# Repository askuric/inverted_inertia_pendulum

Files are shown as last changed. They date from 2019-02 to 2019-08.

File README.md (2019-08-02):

# Inertia Wheel Inverted Pendulum Project 

This project is suitable for anyone with extra free time and passion for interesing projects, but especially for electrical engineering studets (contorl theory students) to learn the control approach of an unstable process and test their algorithms, the primary contorller used in this project is LQR.  

This project is also available on [Thingiverse](https://www.thingiverse.com/thing:3422949)

This project is based on Nucleo STM32F411RE microcontroller. And the repo contains :
- CubeMX project 
- Keil project
- Solidworks files and STLs

YouTube link:<br>
 IMAGE ALT TEXT HERE (https://www.youtube.com/watch?v=POPPNbzDYbw)
 
The full gallery of the project can be found on [Link](https://photos.app.goo.gl/RDtYy89tumxfFMtH9):
<p>


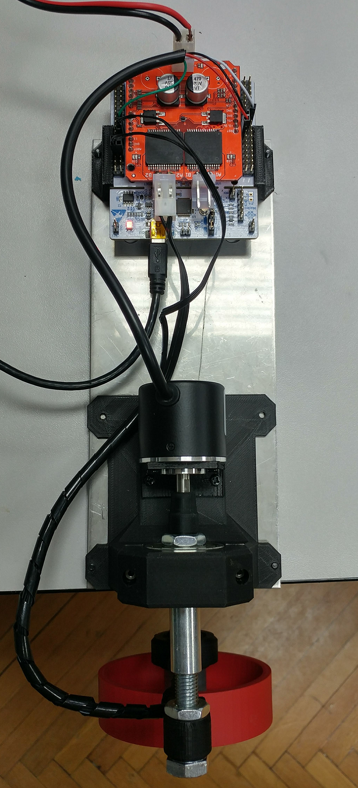
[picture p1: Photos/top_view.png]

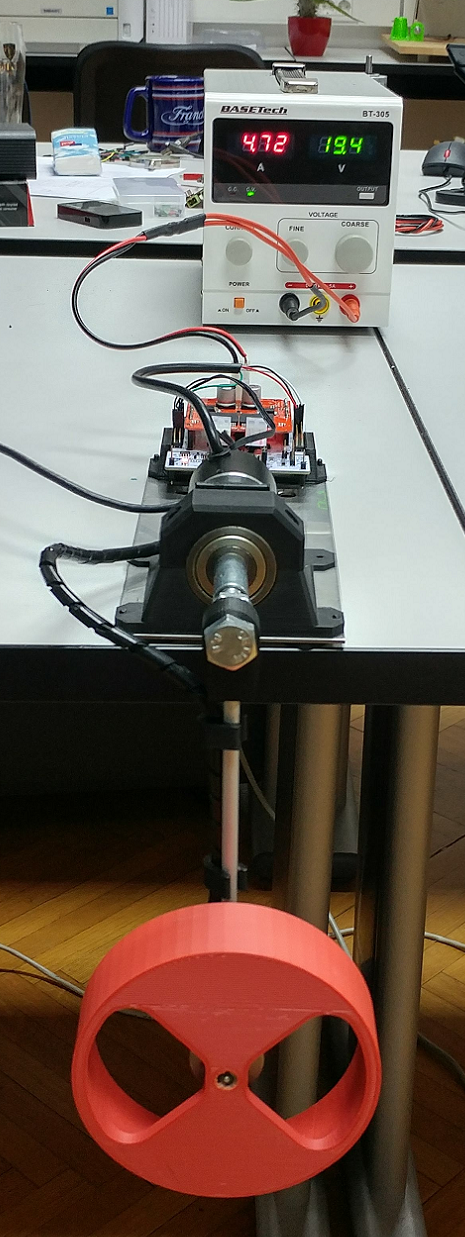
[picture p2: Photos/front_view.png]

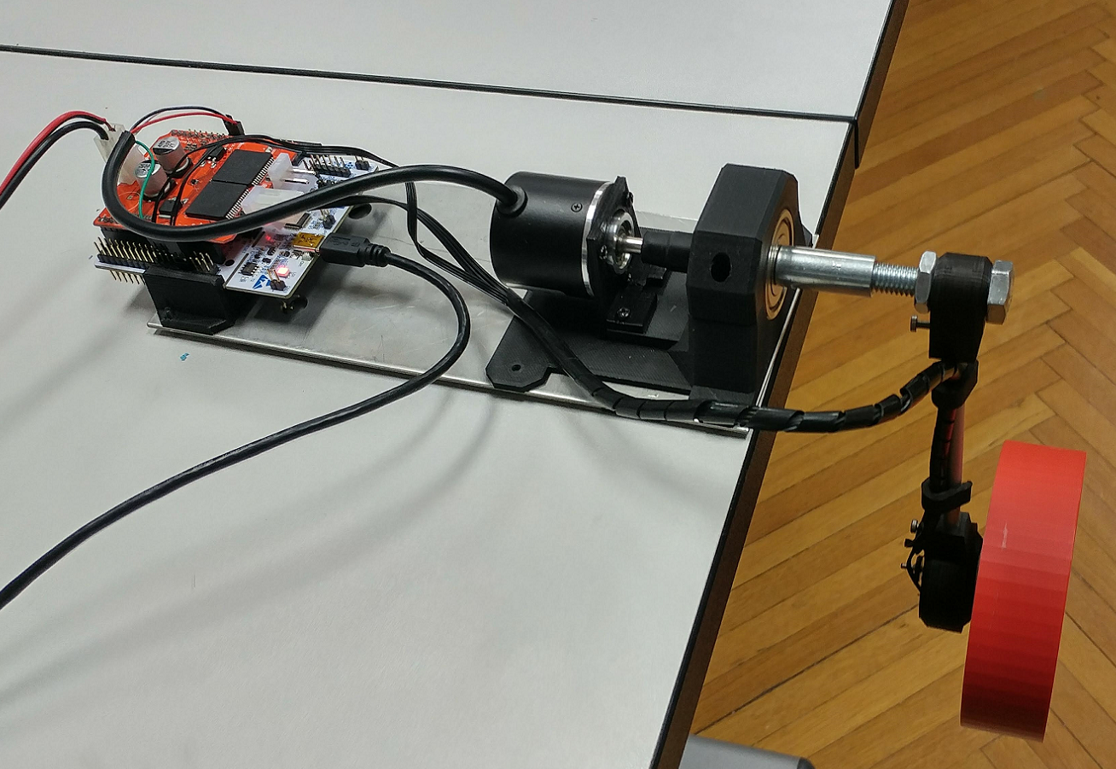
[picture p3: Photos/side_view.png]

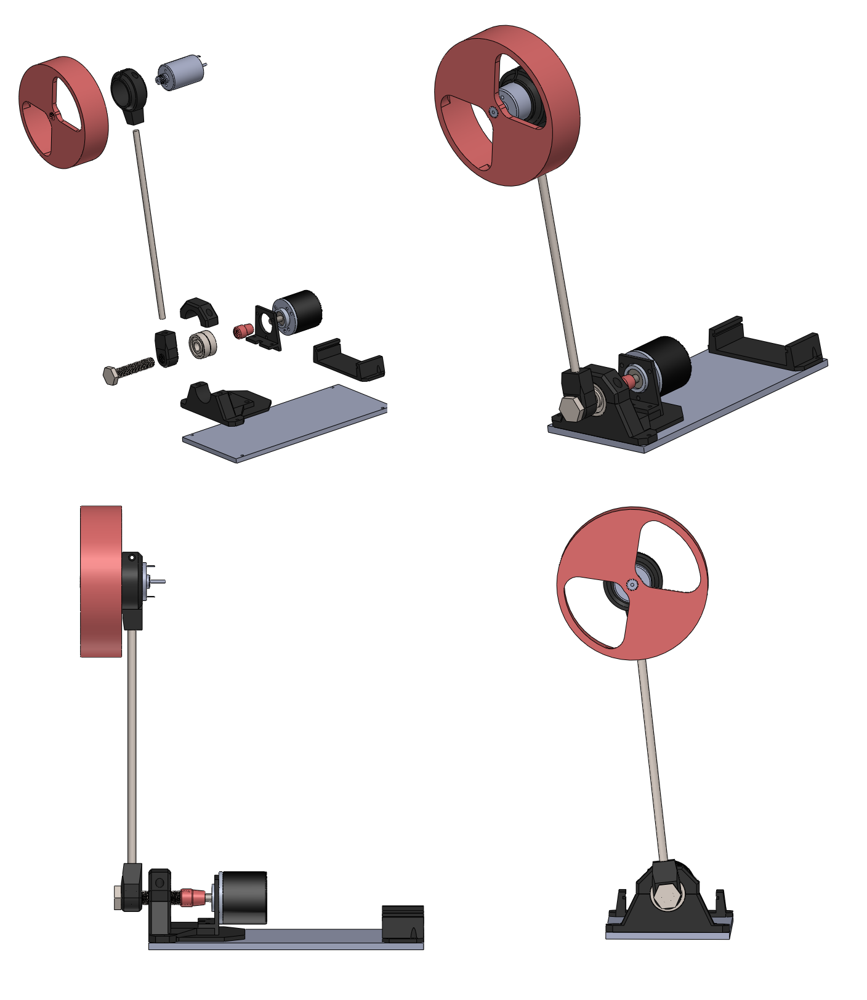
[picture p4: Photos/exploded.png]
</p>

# Electronics hardware
- Nuceleo STM32F411RE - [Mouser](https://hr.mouser.com/ProductDetail/STMicroelectronics/NUCLEO-F411RE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) 
- Monster motor shield - [Ebay](https://www.ebay.com/itm/L298N-Dual-VNH2SP30-Stepper-Motor-Driver-Module-30A-Monster-Moto-Shield-Replace/112031018900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)
- Motor - Mabuchi RS-385PH with encoder (hall or optical)
  -  With encoder or hall sensors  [Ebay](https://www.ebay.com/itm/RS-385PH-16140-MABUCHI-DC-24V-Motor-for-Printer-Copy-machine/222827327725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)
  -  I used motor without sensor and retrofited it with Hall encoder 20cpr [Ebay](https://www.ebay.com/itm/Pololu-Romi-Encoder-Pair-Kit-12-CPR-3-5-18V-with-Hall-effect-sensor-3542/272789024914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)
- Encoder [Aliexpress](https://www.aliexpress.com/item/360-600P-R-Photoelectric-Incremental-Rotary-Encoder-5-24V-AB-Two-Phases-Shaft/32756209569.html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,searchweb201602_1_10065_10068_319_10059_10884_317_10887_10696_321_322_453_10084_454_10083_10103_10618_10307_10820_10301_10821_10303_537_536_10902,searchweb201603_45,ppcSwitch_0&algo_expid=3179dab4-6711-42f4-8e94-b644142c4211-5&algo_pvid=3179dab4-6711-42f4-8e94-b644142c4211)
- 1x 6mm steel or aluminum rod, 120mm long 
- 1x M10x1.5 screw 
- 2x M10x1.5 nuts
- 10x M3 screw 
- 10x M3 Brass Knurl Nuts [Aliexpress](https://www.aliexpress.com/item/100pcs-Brass-Knurl-Nuts-M3x4mm-L-5mm-OD-Metric-Threaded-insert/1294839803.html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)
- 2x ball bearing, 10mm x 35mm x 11mm 
- steel/amulinum/wooden plate (cca 90mm x 2mm x300mm)

# 3D printed parts
-  Inetria wheel - (0.1mm | 50+%)
   - Motor shaft mount has to be adapted
   - The two provided wheel STLs are for 14tooth and 12tooth version of motors
   - Feel free to make your own version of the inertia wheel with the solidworks file
-  Motor mount - (0.2mm | 30%)
-  Pole shaft connector - (0.1mm | 30%)
-  Shaft adapter - (0.1mm | 30%)
-  Table mount + bearing holder - (0.2mm | 30%)
-  Nucleo mount - (0.2mm | 30%)

# Control algorithm
 - PD (Simple)
 - LQR algorithm (Intermediate) - <b>Included in the software + Synthesis using Matlab scirpt</b>
 - MPC (Advanced) - Suggested use of [muao MPC](http://ifatwww.et.uni-magdeburg.de/syst/muAO-MPC/)

# Connecting the hardware
 - Monster motor shield is mounted on nucleo very simply, as on any Arduino
    - It provides the hardware connections needed and no need for additional jumpers
    - Inertia wheel motor should be connected to motor 2 terminal
    - 18V - 5A power supply should be used to power the shield
 - Encoder connection diagram is as follows:
 
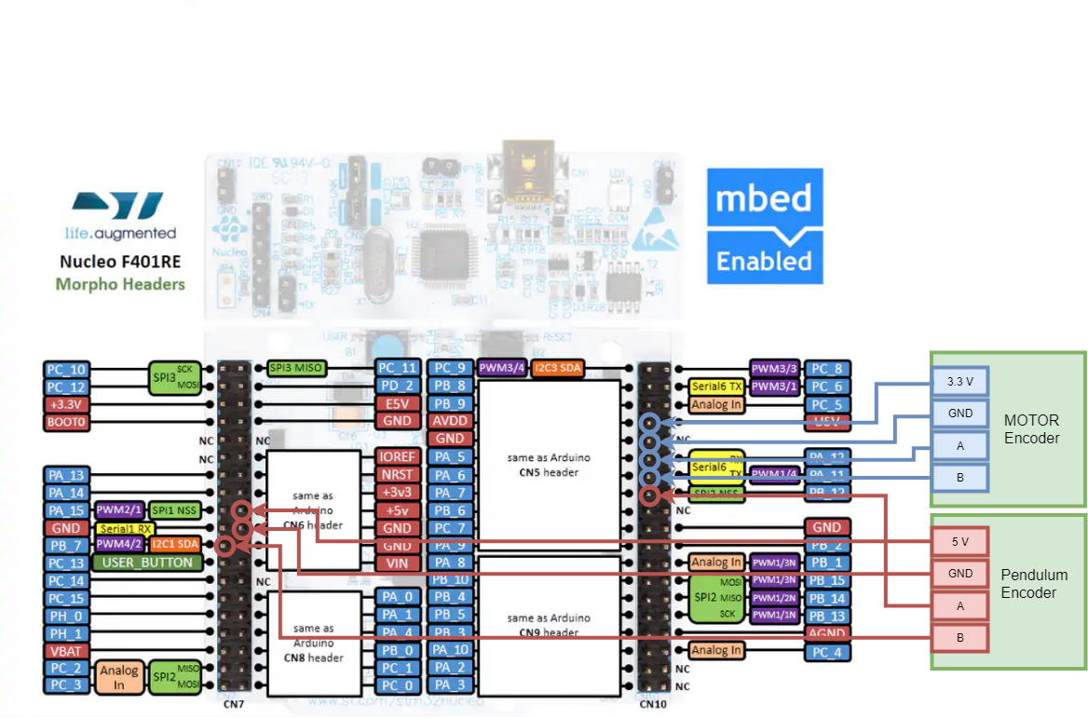
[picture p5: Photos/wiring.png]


# Running the code
 - Build the Keil project and download it to your Nucleo

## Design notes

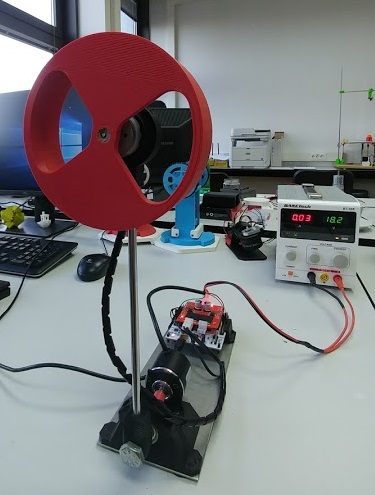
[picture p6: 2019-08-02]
Photos/pendulum3.jpg

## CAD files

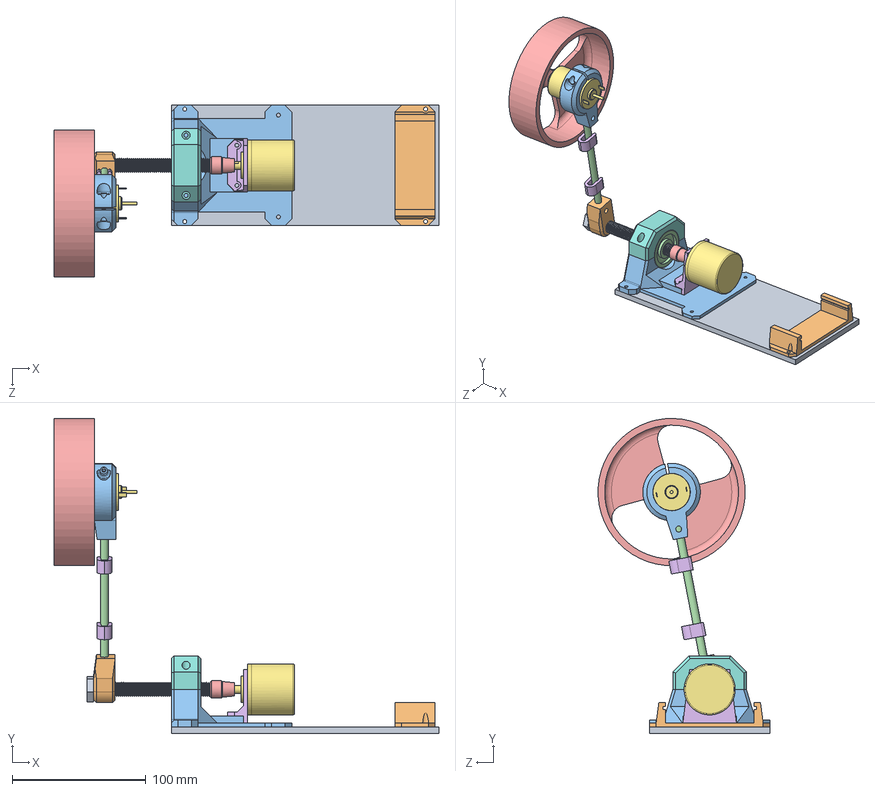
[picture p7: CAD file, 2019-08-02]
CAD/pendulum.SLDASM
287.7 x 235.4 x 128.4 mm
bottom_plate
nucleo_holder
table_mount
radial ball bearing_68_iso x 2
axel_adapter_10mm_encoder
encoder_holder
encoder
bearing_holder
bolt
mount_table_sharft_holder
motor_mout_mabuchi
pole
mabuchi_wheel_14T
cable_holder x 2
MABUCHI RS-385

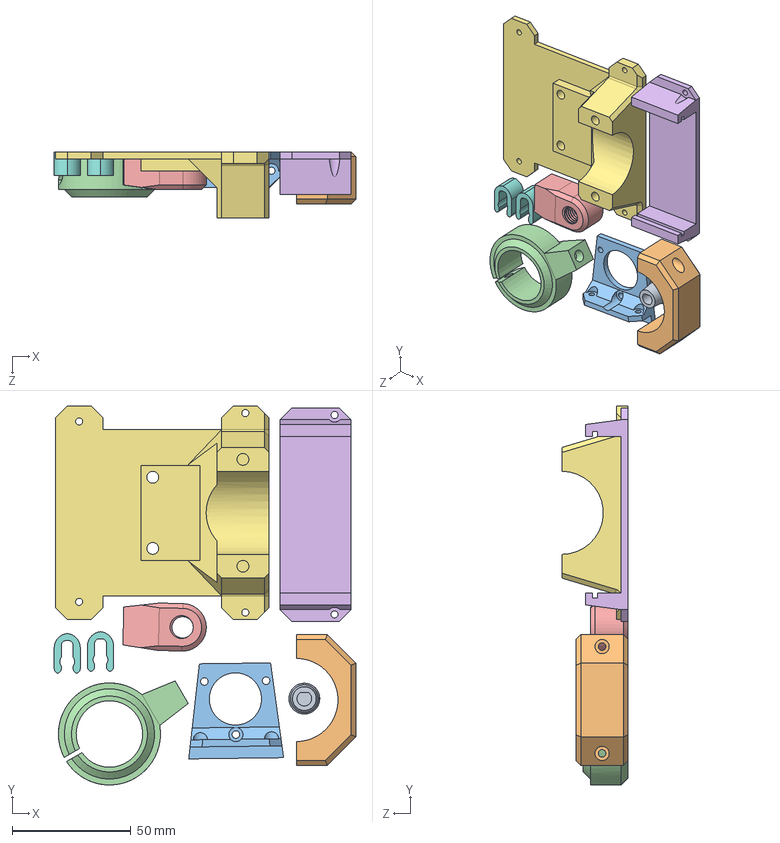
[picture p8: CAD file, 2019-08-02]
CAD/print_layout.SLDASM
127.1 x 159.7 x 28.0 mm
axel_adapter_10mm_encoder
bearing_holder
encoder_holder
motor_mout_mabuchi
mount_table_sharft_holder
nucleo_holder
table_mount
cable_holder x 2

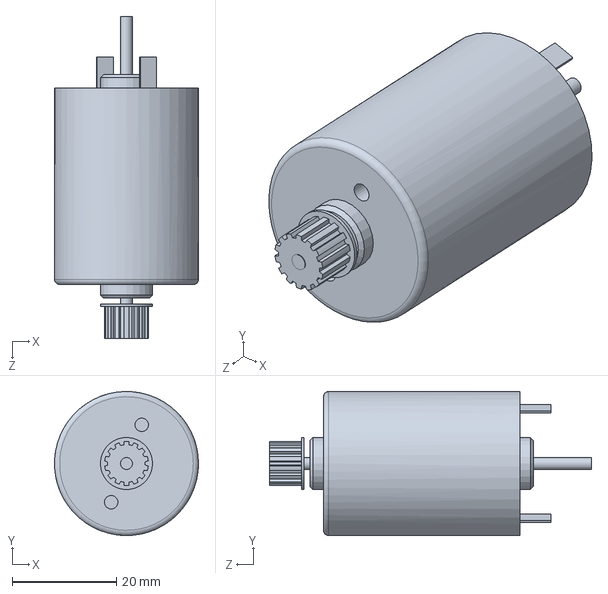
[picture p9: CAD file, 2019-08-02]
CAD/MABUCHI RS-385.SLDPRT
27.7 x 27.7 x 62.0 mm

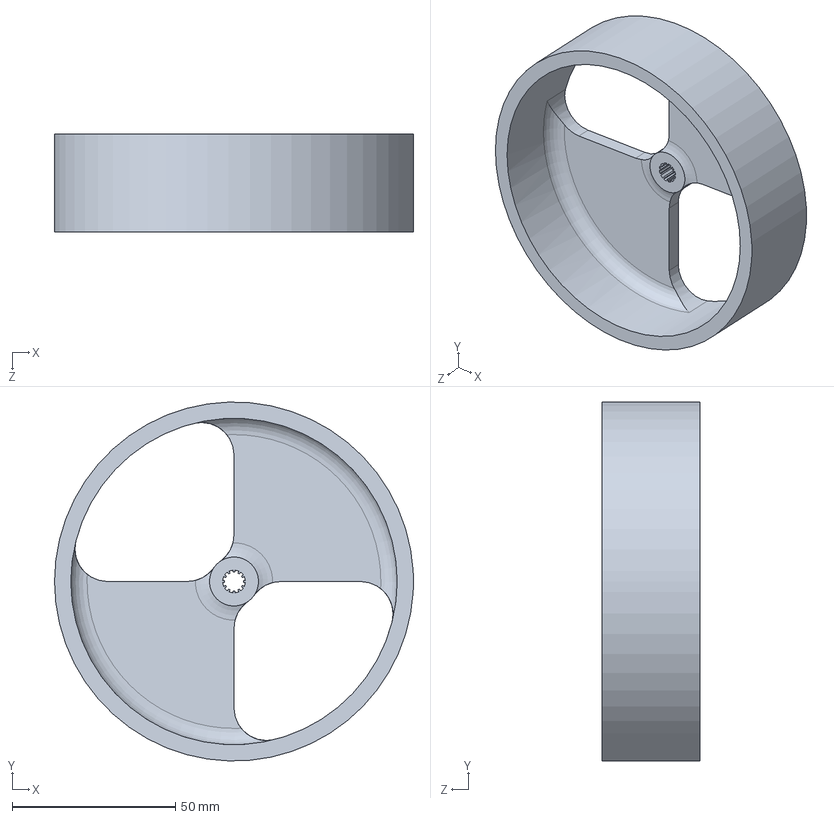
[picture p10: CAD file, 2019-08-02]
CAD/mabuchi_wheel_12T.SLDPRT
110.0 x 110.0 x 30.0 mm

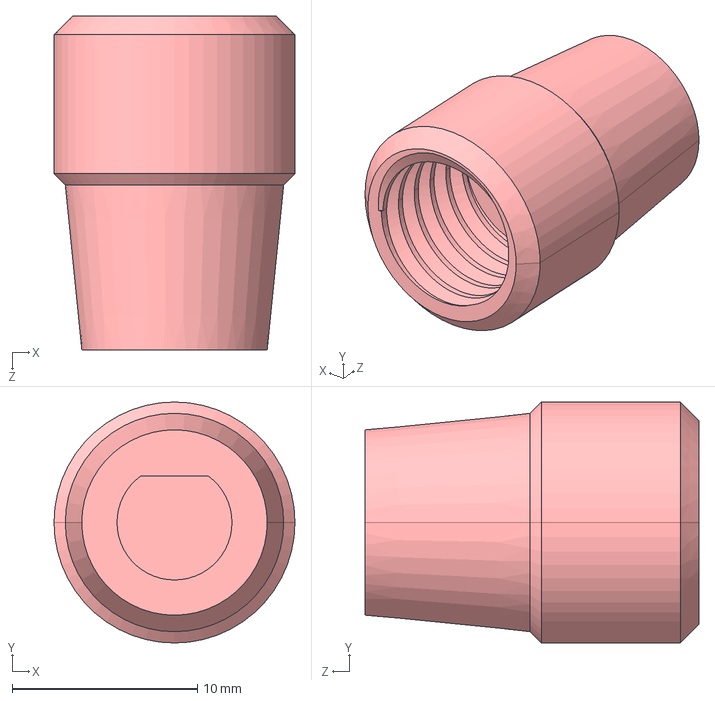
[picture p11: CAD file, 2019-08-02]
CAD/axel_adapter_10mm_encoder.STEP
13.0 x 13.0 x 18.0 mm

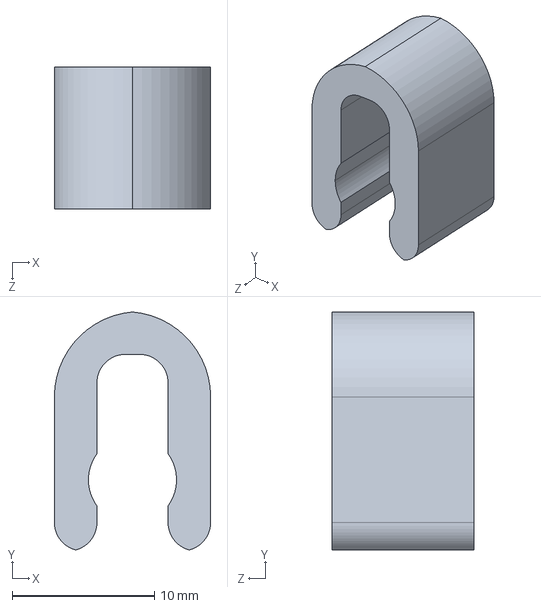
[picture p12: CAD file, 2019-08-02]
CAD/cable_holder.STEP
11.0 x 16.7 x 10.0 mm

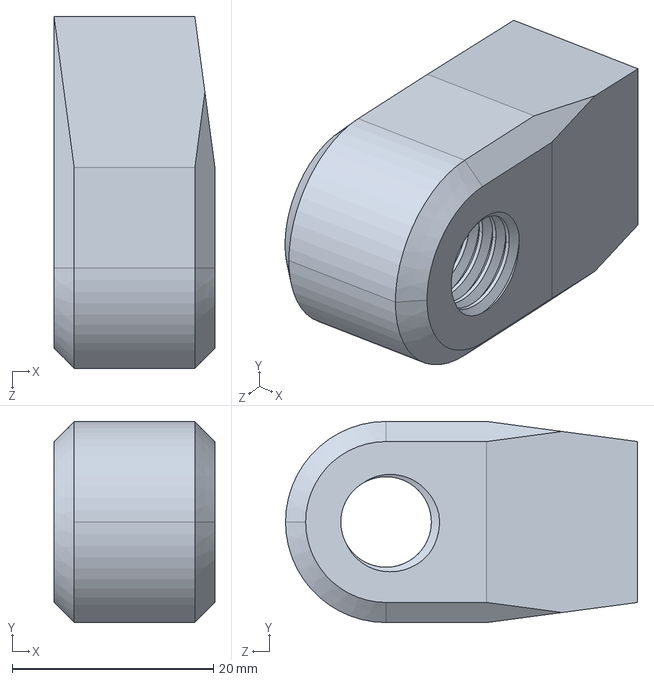
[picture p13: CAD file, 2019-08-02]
CAD/mount_table_sharft_holder.STEP
16.0 x 20.0 x 35.0 mm

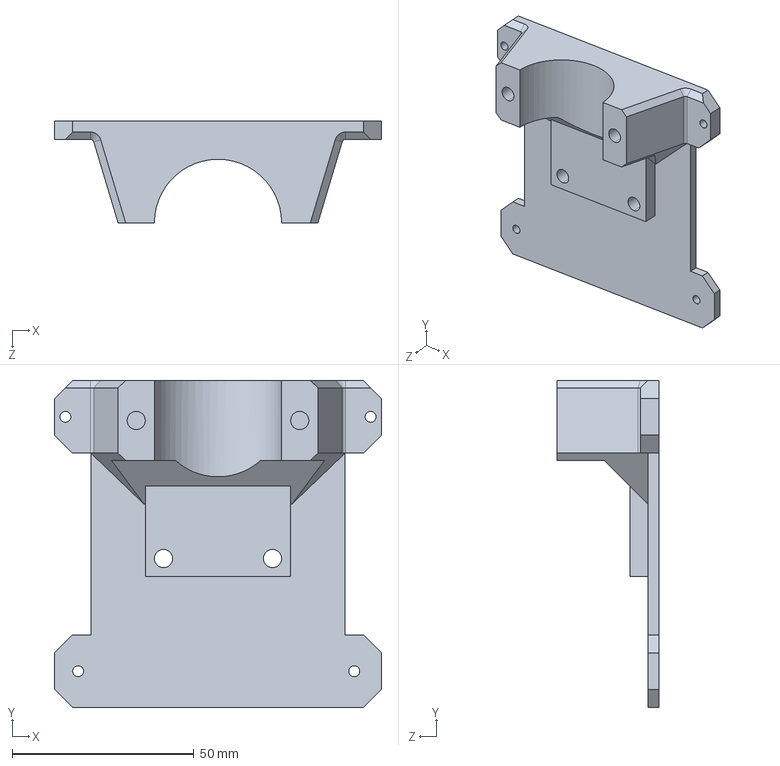
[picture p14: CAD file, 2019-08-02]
CAD/table_mount.STEP
90.0 x 90.0 x 28.0 mm

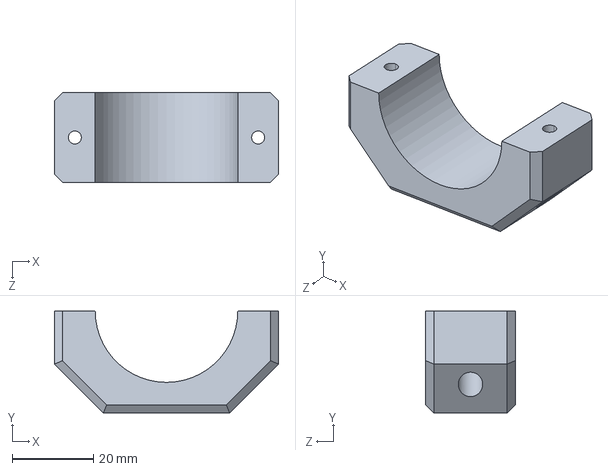
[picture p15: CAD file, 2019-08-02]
CAD/bearing_holder.STEP
55.0 x 25.0 x 22.0 mm

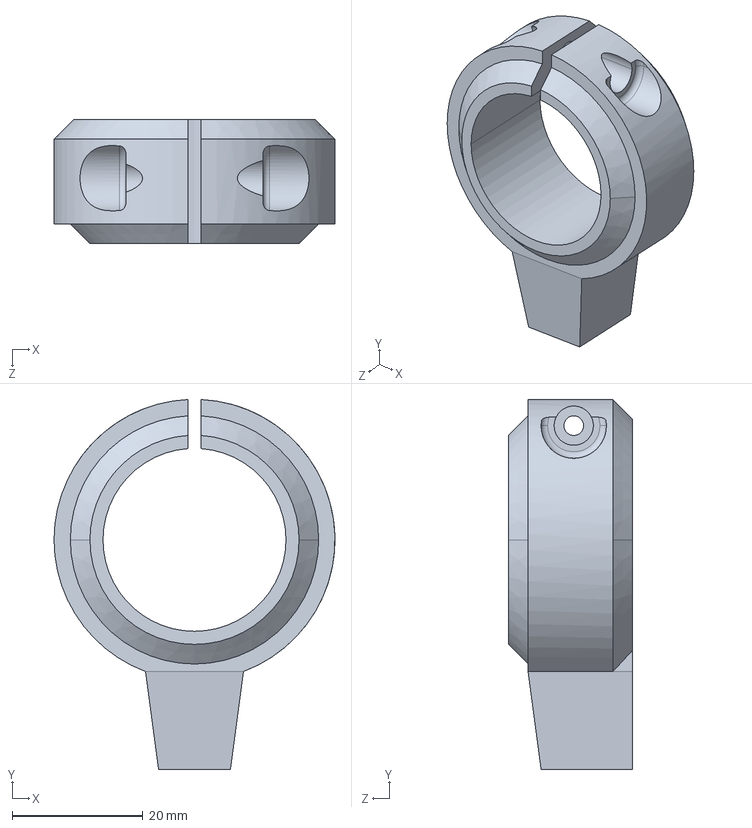
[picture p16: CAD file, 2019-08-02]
CAD/motor_mout_mabuchi.STEP
43.0 x 56.6 x 19.0 mm

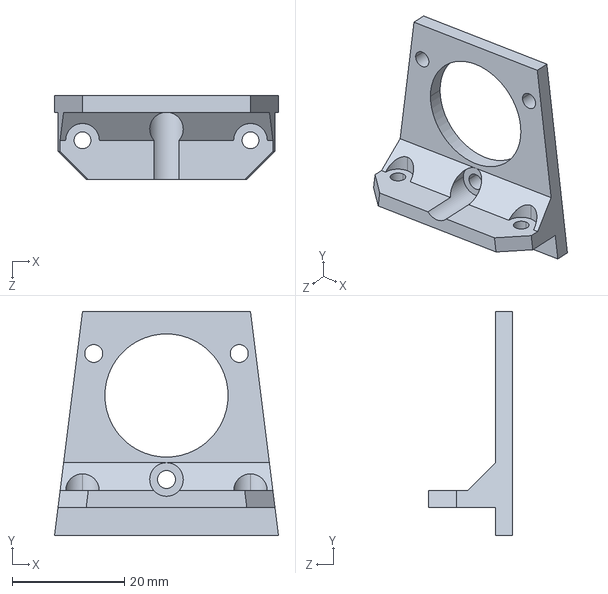
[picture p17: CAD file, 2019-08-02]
CAD/encoder_holder.STEP
40.0 x 40.0 x 15.0 mm

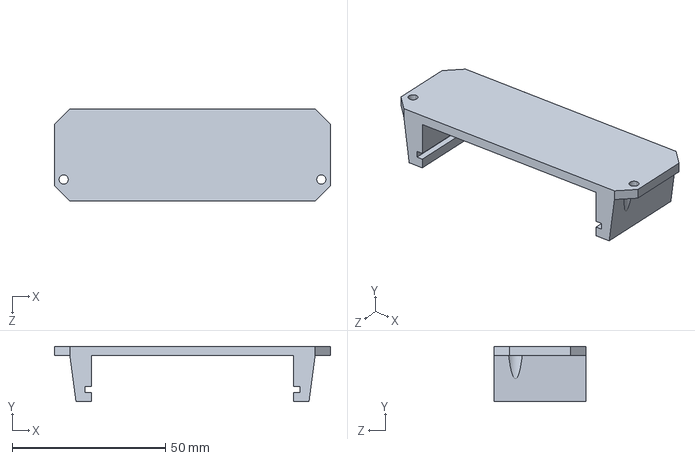
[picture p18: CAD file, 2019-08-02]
CAD/nucleo_holder.STEP
90.0 x 18.0 x 30.0 mm

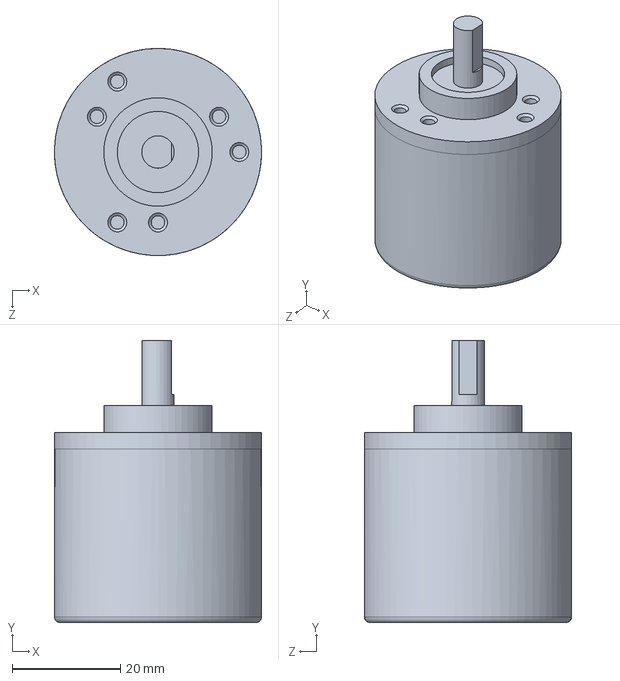
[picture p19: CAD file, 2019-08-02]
CAD/encoder.SLDPRT
38.2 x 52.0 x 38.2 mm

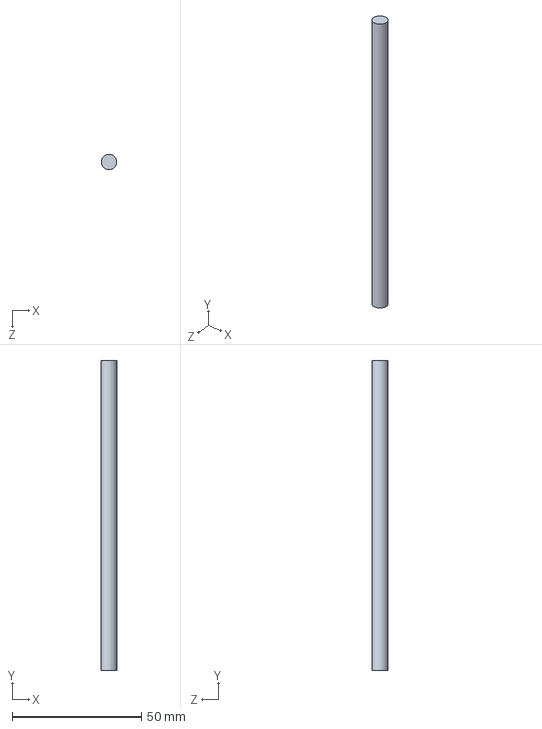
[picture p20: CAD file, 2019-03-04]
CAD/pole.SLDPRT
6.00 x 120.0 x 6.00 mm

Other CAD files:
CAD/mabuchi_wheel_14T.SLDPRT
CAD/bottom_plate.SLDPRT
CAD/bolt.SLDPRT
CAD/axel_adapter_10mm_encoder.SLDPRT
CAD/axel_adapter_10mm_encoder.STL
CAD/bearing_holder.SLDPRT
CAD/bearing_holder.STL
CAD/cable_holder.SLDPRT
CAD/cable_holder.STL
CAD/encoder_holder.SLDPRT
CAD/encoder_holder.STL
CAD/mabuchi_wheel_12T.STL
CAD/mabuchi_wheel_14T.STL
CAD/motor_mout_mabuchi.SLDPRT
CAD/motor_mout_mabuchi.STL
CAD/mount_table_sharft_holder.SLDPRT
CAD/mount_table_sharft_holder.STL
CAD/nucleo_holder.SLDPRT
CAD/nucleo_holder.STL
CAD/print_layout.STL
CAD/table_mount.SLDPRT
CAD/table_mount.STL

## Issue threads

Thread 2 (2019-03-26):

what‘s the infill of 3D printed parts?

18660814995, 2019-03-26:
what‘s the infill of 3D printed parts?

askuric, 2019-03-26:
If you want a quick answer, I would print it with 50% infill and 0.1mm layer height.
 (Layer height | infill density)
Inetria wheel - (0.1mm | 50+%)
  Motor shaft mount has to be adapted
  The two provided wheel STLs are for 14tooth and 12tooth version of motors
  Feel free to make your own version of the inertia wheel with the solidworks file
Motor mount - (0.2mm | 30%)
Pole shaft connector - (0.1mm | 30%)
Shaft adapter - (0.1mm | 30%)
Table mount + bearing holder - (0.2mm | 30%)
Nucleo mount - (0.2mm | 30%)
Thnanks for the feedback, I forgot to put it in.

18660814995, 2019-03-27:
Well done!

Closed 2019-03-30.

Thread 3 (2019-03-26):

what‘s the infill of 3D printed parts?

18660814995, 2019-03-26:
what‘s the infill of 3D printed parts?

askuric, 2019-03-26:
If you want a quick answer, I would print it with 50% infill and 0.1mm layer height.
 (Layer height | infill density)
Inetria wheel - (0.1mm | 50+%)
  Motor shaft mount has to be adapted
  The two provided wheel STLs are for 14tooth and 12tooth version of motors
  Feel free to make your own version of the inertia wheel with the solidworks file
Motor mount - (0.2mm | 30%)
Pole shaft connector - (0.1mm | 30%)
Shaft adapter - (0.1mm | 30%)
Table mount + bearing holder - (0.2mm | 30%)
Nucleo mount - (0.2mm | 30%)

18660814995, 2019-03-27:
Sorry for my mistake,I put 2 issues

Closed 2019-03-30.

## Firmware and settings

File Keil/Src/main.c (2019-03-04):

/**
  ******************************************************************************
  * @file           : main.c
  * @brief          : Main program body
  ******************************************************************************
  ** This notice applies to any and all portions of this file
  * that are not between comment pairs USER CODE BEGIN and
  * USER CODE END. Other portions of this file, whether 
  * inserted by the user or by software development tools
  * are owned by their respective copyright owners.
  *
  * COPYRIGHT(c) 2019 STMicroelectronics
  *
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
  ******************************************************************************
  */
/* Includes ------------------------------------------------------------------*/
#include "main.h"
#include "stm32f4xx_hal.h"

/* USER CODE BEGIN Includes */
#include "pendulum.h"
#include <math.h>
/* USER CODE END Includes */

ADC_HandleTypeDef hadc1;
DMA_HandleTypeDef hdma_adc1;

TIM_HandleTypeDef htim2;
TIM_HandleTypeDef htim3;
TIM_HandleTypeDef htim4;

/* USER CODE BEGIN PV */
float counter,count;

#define ADC_BUFF_SIZE 2
uint32_t adcbuff[2];
/* USER CODE END PV */

void SystemClock_Config(void);
static void MX_GPIO_Init(void);
static void MX_DMA_Init(void);
static void MX_TIM2_Init(void);
static void MX_ADC1_Init(void);
static void MX_TIM4_Init(void);
static void MX_TIM3_Init(void);
                                    
void HAL_TIM_MspPostInit(TIM_HandleTypeDef *htim);
                                

/* USER CODE BEGIN PFP */

/* USER CODE END PFP */

/* USER CODE BEGIN 0 */
void Controller_SysTick(){
	static int n_m,n_p;
	
	if(n_m >= (M_Ts*1000)){
		// gather state variables
		motor_variables_iter();
		n_m=0;
	}else{
		n_m++;
	}
	if(n_p >= (P_Ts*1000)){
		pendulum_variables_iter();
		
		if(fabs(pendulum.position) < P_SWITCH_ANGLE){
			pendulum_LQR();
			//pendulum_P();
		}else{
			pendulum_swingup();
			//pendulum_disable();
		}
		n_p = 0;
	}else{
		n_p++;
	}
}
/* USER CODE END 0 */

/**
  * @brief  The application entry point.
  *
  * @retval None
  */
int main(void)
{
  /* MCU Configuration----------------------------------------------------------*/

  /* Reset of all peripherals, Initializes the Flash interface and the Systick. */
  HAL_Init();

  /* Configure the system clock */
  SystemClock_Config();

  /* Initialize all configured peripherals */
  MX_GPIO_Init();
  MX_DMA_Init();
  MX_TIM2_Init();
  MX_ADC1_Init();
  MX_TIM4_Init();
  MX_TIM3_Init();
  /* USER CODE BEGIN 2 */

	// init encoders
	HAL_TIM_Encoder_Start(&htim4,TIM_CHANNEL_ALL);
	HAL_TIM_Encoder_Start(&htim3,TIM_CHANNEL_ALL);
	
	// init PWM
	HAL_TIM_PWM_Start(&htim2,TIM_CHANNEL_3);
	
  /* USER CODE END 2 */

  /* Infinite loop */
  /* USER CODE BEGIN WHILE */
  while (1)
  {
		
		// no code in while loop, everything is in the function SysTick_Handler() in the stm32f4xx_it.c
  /* USER CODE END WHILE */

  /* USER CODE BEGIN 3 */

  }
  /* USER CODE END 3 */

}

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


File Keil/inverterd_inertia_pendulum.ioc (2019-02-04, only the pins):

Mcu.UserName=STM32F411RETx
PA0-WKUP.GPIO_Label=M1_EN
PA0-WKUP.Signal=GPIO_Output
PA1.GPIO_Label=M2_EN
PA1.Signal=GPIO_Output
PA4.Signal=ADCx_IN4
PA6.Signal=S_TIM3_CH1
PA7.Signal=S_TIM3_CH2
PA8.GPIO_Label=M1_CW
PA8.Signal=GPIO_Output
PA9.GPIO_Label=M1_CCW
PA9.Signal=GPIO_Output
PB0.Signal=ADCx_IN8
PB10.GPIO_Label=M2_PWM
PB10.Signal=S_TIM2_CH3
PB5.GPIO_Label=M2_CW
PB5.Signal=GPIO_Output
PB6.Signal=S_TIM4_CH1
PB7.Signal=S_TIM4_CH2
PC7.GPIO_Label=M2_CCW
PC7.Signal=GPIO_Output

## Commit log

2019-02-04 added CAD files
    [1.sldprt, 10.sldprt, 11.sldprt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]
2019-02-07 updated cad files
    [1.sldprt, 10.sldprt, 11.sldprt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]
2019-02-12 added matlab script
    [full_pendulum.SLDASM]
2019-02-13 updated screw thread settings to M10x1.5
    [axel_adapter_10mm_encoder.SLDPRT, axel_adapter_10mm_encoder.STL, bolt.SLDPRT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]
2019-03-04 matlab update - added simulink model
    [bearing_holder.SLDPRT, bearing_holder.STL, bolt.SLDPRT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]
2019-08-02 FEATURE Added the step files and done the cleanup of CAD models
    [axel_adapter_10mm_encoder.SLDPRT, axel_adapter_10mm_encoder.STEP, axel_adapter_10mm_encoder.STL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]
2019-08-02 FIX Rename Solidworks to CAD
    [11.sldprt, MABUCHI RS-385.SLDASM, axel_adapter_10mm_encoder.SLDPRT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]
2019-08-02 UPDATE Final CAD cleanup
    [11.sldprt, MABUCHI RS-385.SLDASM, MABUCHI RS-385.SLDPRT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]

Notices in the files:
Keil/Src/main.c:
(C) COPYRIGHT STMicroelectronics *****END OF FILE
